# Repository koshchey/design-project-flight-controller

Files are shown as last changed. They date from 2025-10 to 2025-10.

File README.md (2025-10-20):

# Indoor Surveillance Drone – ELEC5552 Team 04 (UWA)

**Authors:** Sofia Khokhlenok (23099635), Sunny Guo (23345534)  
**Unit:** ELEC5552  
**Project Partners:** Michal Zawierta & Dilusha Silva, UWA Aviation Labs  
**Supervisor:** Jega Gurusamy  
**Team Number:** 04  

*Final Design Report - Version 2*

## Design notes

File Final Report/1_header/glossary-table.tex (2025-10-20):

\section*{Acronyms}
\renewcommand{\arraystretch}{1.2} % optional: adjust row spacing

\begin{tabular}{p{0.2\textwidth} p{0.3\textwidth} | p{0.2\textwidth} p{0.3\textwidth}}
\textbf{Acronym} & \textbf{Definition} & \textbf{Acronym} & \textbf{Definition} \\
\hline
IMU & Inertial Measurement Unit & UAV & Unmanned Aerial Vehicle \\
ToF & Time-of-Flight Sensor & UWAAL & UWA Aviation Labs \\
I\textsuperscript{2}C & Inter-Integrated Circuit & PCB & Printed Circuit Board \\
SPI & Serial Peripheral Interface & IR & Infrared \\
UWA & The University of Western Australia & QFD & Quality Function Deployment \\
LiPo & Lithium Polymer battery & NGO & Need, Goals, Objectives \\
PWM & Pulse Width Modulation & GPS & Global Positioning System \\
ESD & Electrostatic Discharge & MCU & Microcontroller \\
ESP32 & Espressif ESP32-Wroom Microcontroller & USB & Universal Serial Bus \\
MPU6050 & MEMS Accelerometer and Gyroscope IC & DC & Direct Current \\
wpa2 & Wi-Fi Protected Access 2 & ESP-IDF & Espressif IoT Development Framework \\
PID & Proportional-Integral-Derivative & RTOS & Real Time Operating System \\
IC & Integrated Circuit & MOSFET & Metal-Oxide-Semiconductor FET \\
AHRS & Attitude and Heading Reference System & UART & Universal Asynchronous RX/TX \\
EMI & Electromagnetic Interference & SCL & Serial Clock Line \\
SDA & Serial Data Line & LDO & Low Dropout Regulator \\
JST & Japan Solderless Terminal Connector & LED & Light Emitting Diode \\
FOV & Field of View & PETG & Polyethylene Terephthalate Glycol \\
RF & Radio Frequency & RC & Resistor-Capacitor \\
ISR & Interrupt Service Routine & ESC & Electronic Speed Controller \\
HTML & HyperText Markup Language &  &  \\
\end{tabular}

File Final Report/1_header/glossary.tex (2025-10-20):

\newacronym{imu}{IMU}{Inertial Measurement Unit}
\newacronym{tof}{ToF}{Time-of-Flight Sensor}
\newacronym{i2c}{I\textsuperscript{2}C}{Inter-Integrated Circuit}
\newacronym{spi}{SPI}{Serial Peripheral Interface}
\newacronym{uwa}{UWA}{The University of Western Australia}
\newacronym{lipo}{LiPo}{Lithium Polymer battery}
\newacronym{pwm}{PWM}{Pulse Width Modulation}
\newacronym{esd}{ESD}{Electrostatic Discharge}
\newacronym{esp32}{ESP32}{Espressif ESP32-Wroom Microcontroller Module}
\newacronym{mpu6050}{MPU6050}{MEMS Accelerometer and Gyroscope IC}
\newacronym{uav}{UAV}{Unmanned Aerial Vehicle}
\newacronym{uwaal}{UWAAL}{UWA Aviation Labs}
\newacronym{pcb}{PCB}{Printed Circuit Board}
\newacronym{ir}{IR}{Infrared}
\newacronym{qfd}{QFD}{Quality Function Deployment}
\newacronym{ngo}{NGO}{Need, Goals, Objectives}
\newacronym{gps}{GPS}{Global Positioning System}
\newacronym{mcu}{MCU}{Microcontroller}
\newacronym{usb}{USB}{Universal Serial Bus}
\newacronym{dc}{DC}{Direct Current}
\newacronym{wpa2}{WPA2}{Wi-Fi Protected Access 2}
\newacronym{esp-idf}{ESP-IDF}{Espressif IoT Development Framework}
\newacronym{pid}{PID}{Proportional-Integral-Derivative}
\newacronym{rtos}{RTOS}{Real Time Operating System}
\newacronym{ic}{IC}{Integrated Circuit}
\newacronym{mosfet}{MOSFET}{Metal-Oxide-Semiconductor Field-Effect Transistor}
\newacronym{ahrs}{AHRS}{Attitude and Heading Reference System}
\newacronym{uart}{UART}{Universal Asynchronous Receiver/Transmitter}
\newacronym{emi}{EMI}{Electromagnetic Interference}
\newacronym{scl}{SCL}{Serial Clock Line}
\newacronym{sda}{SDA}{Serial Data Line}
\newacronym{ldo}{LDO}{Low Dropout Regulator}
\newacronym{jst}{JST}{Japan Solderless Terminal Connector}
\newacronym{led}{LED}{Light Emitting Diode}
\newacronym{fov}{FOV}{Field of View}
\newacronym{petg}{PETG}{Polyethylene Terephthalate Glycol}
\newacronym{rf}{RF}{Radio Frequency}
\newacronym{rc}{RC}{Resistor-Capacitor}
\newacronym{isr}{ISR}{Interrupt Service Routine}
\newacronym{esc}{ESC}{Electronic Speed Controller}
\newacronym{html}{HTML}{HyperText Markup Language}

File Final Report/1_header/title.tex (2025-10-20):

\begin{titlepage}

\noindent\rule{\textwidth}{0.5pt}
\begin{flushright}
    \textbf{UWA ELEC5552}
\end{flushright}
\rule{\textwidth}{0.5pt}

\vspace{2cm}

\thispagestyle{empty}

\begin{center}
    {\Huge \textbf{Indoor Surveillance Drone}} \\[0.75cm]
    {\Large ELEC5552 Team 04} \\[1.5cm]

    \textsc{Author(s):} \\[0.5cm]

    \begin{tabular}{@{}c@{\hskip 1cm}c@{}}
        \textbf{Sofia Khokhlenok} & \textbf{Sunny Guo} \\[0.2cm]
        (23099635) & (23345534) \\
    \end{tabular} \\[1.5cm]

    {\Large \textbf{Final Design Report}} \\[0.5cm]
\end{center}

\vspace{1.5cm}

\begin{center}
\begin{tabular}{rl}
\textsc{Project Partners:} & Michal Zawierta \& Dilusha Silva, UWA Aviation Labs \\
\textsc{UWA Supervisor:} & Jega Gurusamy \\
\textsc{Team Number:} & 04 \\
\textsc{Meeting Time:} & Thursday, 10AM \\
\textsc{Word Count:} & 8568 \\
\textsc{Word Limit:} & 10~000 \\
\textsc{Version:} & 2 \\
\end{tabular}
\end{center}

\vfill

\begin{center}
    \large \today
\end{center}

\end{titlepage}

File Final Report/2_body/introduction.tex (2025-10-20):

\glspl{uav}, commonly referred to as drones, have become essential tools across a wide range of applications, including surveying, inspection, and research. Their ability to operate in confined or inaccessible environments makes them particularly valuable for close-range observation and monitoring tasks. Unlike outdoor drones that rely on satellite-based positioning systems such as GPS, indoor platforms must depend entirely on onboard sensing, control algorithms, and communication systems to maintain stability and navigate safely. Operating in enclosed environments presents additional challenges, including limited spatial awareness, airflow disturbances, and increased safety risks due to proximity to structures and personnel. Consequently, the design of an indoor \gls{uav} demands careful consideration of system architecture, control robustness, and physical safety features. 

\begin{figure}[H]
    \centering
    \captionsetup{justification=centering, margin=1cm}
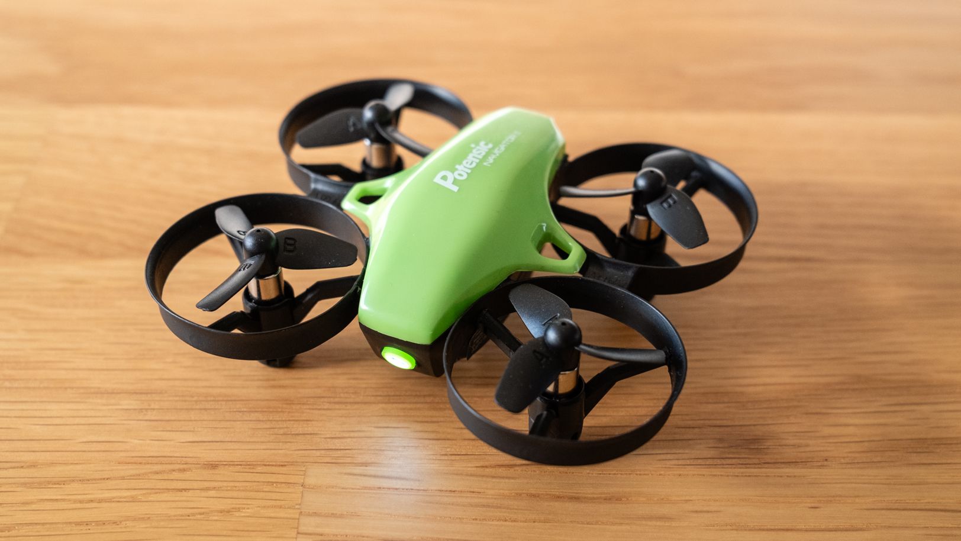
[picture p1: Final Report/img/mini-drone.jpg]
    
    \caption{Miniature Drone \cite{abbott2024}}
\end{figure}

The \gls{uwaal} has commissioned the development of an autonomous indoor drone capable of stable flight within confined environments. The system will be used to survey and inspect indoor areas such as garages and laboratories, following predefined flight paths while maintaining altitude and position despite external airflow disturbances. It must integrate sensing, control, communication, and power management within a compact and lightweight platform, designed from first principles to ensure safety, efficiency, and reliability. This project explores the design and implementation of such a platform, aligning with \gls{uwaal}’s objective to develop a safe, functional, and adaptable indoor drone for future research and educational applications. 

\subsection{Scope of This Report}

This report outlines the process undertaken to design and implement a functional indoor \gls{uav} for operation within confined environments. It defines the technical, safety, and regulatory boundaries within which the project was executed, as well as the methods used to evaluate performance against client-approved requirements. The scope covers system-level design, hardware and firmware integration, testing, and validation to ensure stable flight, effective altitude control, reliable communication, and essential safety functionality. 

The document also presents the rationale behind key design choices and the underlying system architecture. It details specific design aspects, including component selection, \gls{pcb} schematic design and layout, flight control algorithms, and safety mechanisms, while addressing relevant standards for electrical safety, risk management, and compliance. Consideration is given to manufacturability, maintainability, and adherence to cost and resource constraints. Beyond immediate development outcomes, the report establishes a framework that supports future extensions of the platform within the \gls{uwaal}. 

\subsection{Purpose of the Design}

The primary objective of this project is to design, develop, and validate a low-cost indoor drone capable of achieving stable flight and hovering performance without GPS-based navigation. The system is intended for use within the \gls{uwaal} to perform autonomous operations while maintaining a specified altitude and compensating for environmental disturbances such as localised airflow. 

\begin{figure}[H]
    \centering
    \captionsetup{justification=centering, margin=1cm}
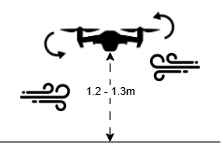
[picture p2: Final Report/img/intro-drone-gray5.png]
    
    \caption{Surveillance Drone Diagram}
\end{figure}

The proposed system architecture features a custom-designed \gls{pcb} flight controller integrating onboard power distribution, sensing, and control modules. Flight stabilisation and altitude control are achieved through sensor fusion of inertial and distance measurements processed via onboard control algorithms. The design incorporates safety features such as shrouded propellers or propeller guards, low-battery auto-landing capability, and a failsafe mechanism that triggers a controlled landing or motor shutdown following a communication loss exceeding thirty seconds. The drone operates on 1S or 2S lithium-polymer batteries with a maximum capacity of 800~mAh and must sustain a minimum flight duration of three minutes. All components and materials conform to the allocated project budget of AUD~\$350. The overarching goal is to deliver a robust, safe, and open-source indoor drone platform that satisfies all operational, safety, and budgetary requirements. 

\subsection{Background}

\glspl{uav} combine sensing, computation, and actuation to achieve controlled flight through coordinated motor thrust. Their operation depends on precise feedback control systems that maintain stability and orientation while responding to pilot or autonomous commands. This is typically accomplished using onboard microcontrollers running real-time control algorithms that process data from inertial and range sensors to dynamically adjust motor outputs.

\begin{figure}[H]
    \centering
    \captionsetup{justification=centering, margin=1cm}
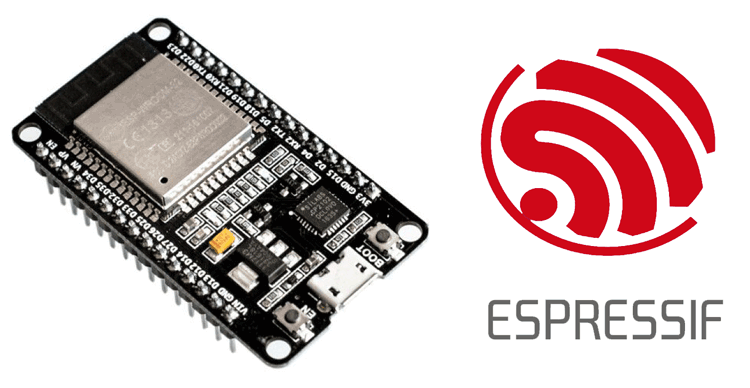
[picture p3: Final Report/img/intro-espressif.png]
    
    \caption{Espressif ESP32 DevKit~\cite{iotdesignpro2019}}
\end{figure}

\pagebreak

The ESP32 microcontroller has emerged as a compact and cost-effective solution for such systems, integrating dual-core processing, Wi-Fi connectivity, and sufficient computational power to manage both flight control and communication tasks. Its compatibility with open-source frameworks such as Espressif’s \gls{esp-idf} enables flexible low-level implementation of control loops, sensor fusion, and telemetry within a single embedded platform.

In parallel, advances in printed circuit board (\gls{pcb}) design allow integration of flight electronics, power management, and motor drivers onto lightweight, custom boards that minimise wiring and improve reliability. 

\begin{figure}[H]
    \centering
    \captionsetup{justification=centering, margin=1cm}
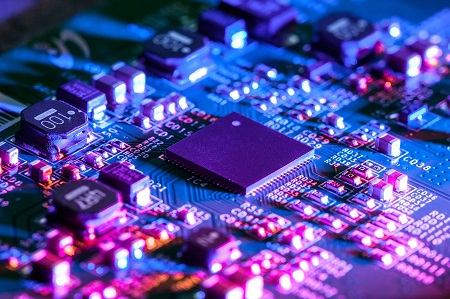
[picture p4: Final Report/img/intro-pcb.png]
    
    \caption{Printed Circuit Board \cite{mistral2020}}
\end{figure}

Together, these developments enable the creation of small-scale, low-cost autonomous drones capable of stable flight and sensor-based navigation for educational, research, and experimental applications.

\subsection{Summary of Contributions}

\begin{table}[H]
\centering
\caption{Team Member Contribution Breakdown}
\renewcommand{\arraystretch}{1.2}
\begin{tabular}{@{}lcc@{}}
\toprule
\textbf{Task} & \textbf{Sofia Khokhlenok (\%)} & \textbf{Sunny Guo (\%)} \\ 
\midrule
Conception & 50 & 50 \\
Research & 60 & 40 \\
Requirement Development & 50 & 50 \\
System Design & 70 & 30 \\
System Architecture & 50 & 50 \\
Hardware Development & 20 & 80 \\
Firmware Development & 90 & 10 \\
PCB Research & 40 & 60 \\
PCB/Frame Prototyping & 20 & 80 \\
Purchasing Electronic Materials & 50 & 50 \\
Frame Design & 15 & 85 \\
Software Debugging and Testing & 80 & 20 \\
Hardware Debugging and Testing & 20 & 80 \\
Overall Prototype Testing & 50 & 50 \\
Management and Organization & 80 & 20 \\
Final Report & 55 & 45 \\
\textbf{Average} & 50 & 50 \\
\bottomrule
\end{tabular}
\end{table}

\subsection{Report Structure}
This report provides a comprehensive overview of the design, development, and evaluation of the autonomous ESP32-based indoor surveillance drone. 

\textbf{Section~1} introduces the project, outlining its scope, purpose, background, and summary of contributions. It also describes the overall report structure to guide the reader. 

\textbf{Section~2} presents the detailed design process, including system requirements, overall and subsystem architecture (hardware, firmware, and justification), and individual design elements such as PCB components, frame design, and firmware modules. It further describes testing procedures—covering hardware verification, stationary and dynamic testing—as well as system integration, stakeholder engagement, safety, ethical considerations, and risk analysis. The section concludes with assembly procedures, design outputs, and final cost breakdowns.

\textbf{Section~3} outlines recommendations for future improvements and potential extensions of the system. 

\textbf{Section~4} serves as a user manual, providing detailed instructions for operation, maintenance, and troubleshooting. 

\textbf{Section~5} lists all referenced materials and supporting documentation. 

Finally, \textbf{the Appendices} contain supplementary materials, including design constraints, requirements updates, prototype details, additional figures, and complete firmware source code listings.

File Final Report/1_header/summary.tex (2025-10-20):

The project presents the design and implementation of an autonomous indoor \gls{uav} for the \gls{uwaal}. The system is intended to operate safely in confined spaces, such as laboratories and workshops, performing inspection and monitoring tasks without reliance on \gls{gps}. The drone integrates sensing, control, communication, and power management on a compact platform built around a custom \gls{pcb} and an \gls{esp32} running the \gls{esp-idf} framework. Key features include stabilisation control systems, onboard sensor fusion, a modular frame with propeller guards, and a real-time telemetry and control interface.

All hardware and firmware subsystems have been implemented and verified individually. The architecture, control logic, and safety mechanisms operate as intended; however, stable flight has not yet been achieved due to motor inconsistencies and limited dynamic testing. With motor replacement, \gls{pid} tuning, and further validation, the system is expected to meet its performance and safety objectives. The project establishes a solid foundation for ongoing development, providing a functional and extensible platform for future research within the \gls{uwaal}.

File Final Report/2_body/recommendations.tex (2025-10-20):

As of the writing of this report, the drone prototype is not yet capable of stable flight. All essential subsystems and components have been implemented and verified individually. The hardware has been tested and is operational, except for some inconsistencies with the motors, which may require replacement. The firmware architecture and control logic function correctly; however, the closed-loop performance of the \gls{pid} controller has not been validated due to limited testing opportunities. With further refinement and testing, the project goals can be fully achieved.

\subsection*{Recommendations for Achieving Project Goals}

\begin{itemize}
    \item \textbf{Motor Replacement and Testing:} Replace the motors and conduct testing to ensure sufficient thrust and balanced torque. Document results in the Verification and Validation (V\&V) table.
    
    \item \textbf{PID Tuning:} Perform PID tuning under hover conditions once stable thrust is achieved. Adjust gains incrementally and log system responses to optimise stability and control.
    
    \item \textbf{Assembly and Connectivity:} Simplify the mechanical and electrical assembly. Use modular connectors or streamlined wiring layouts to reduce manual work and improve reliability.
    
    \item \textbf{Sensor Upgrade:} Consider replacing the \gls{mpu6050} with a more modern \gls{imu} to improve data accuracy, reduce noise, and enhance stability during flight.
    
    \item \textbf{Future Hardware Improvements:} Evaluate brushless motors, electronic speed controllers (\gls{esc}), and higher-voltage batteries to improve thrust and control precision while maintaining safety with the current frame and software limits.
\end{itemize}

Overall, the system foundation is solid. With incremental hardware replacements, \gls{pid} optimisation, and moderate design refinements, the drone can achieve stable and reliable flight and meet the original project objectives.

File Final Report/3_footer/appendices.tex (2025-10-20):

\subsection{Constraints}
\label{app:constraints}

\begin{table}[H]
\centering
\caption{Constraints for Drone Design (Updated)}
\label{tab:constraints}
\begin{tabular}{|>{\centering\arraybackslash}p{0.05\textwidth} | >{\centering\arraybackslash}p{0.13\textwidth} | p{0.42\textwidth} | p{0.30\textwidth}|}
\hline
\rowcolor{gray!15}
\textbf{No.} & \textbf{Constraint} & \textbf{Description} & \textbf{Assumptions} \\
\hline
C.1 & Weight & The total weight of the drone must allow for continuous and stable flight. & The quad-mounted motors can support a maximum payload of 60\,g. \\
\hline
C.2 & Software & Only free and open-source flight controller software shall be used. & The firmware will incorporate third-party open-source code, which will be modified to suit the application (e.g., autonomy and feedback). \\
\hline
C.3 & Operating Environment & The drone is limited to operation within a fixed indoor area containing immovable fixtures (e.g., wall-mounted displays). & -- \\
\hline
C.4 & Budget & The design and construction of the drone shall remain within the allocated project budget. & -- \\
\hline
C.5 & Network Speed & Wireless bandwidth and latency may limit the system’s ability to stream live video. & Streaming will occur via \gls{uwa} Wi-Fi or a mobile hotspot. \\
\hline
C.6 & Safety & The drone must be safe for operation by the user and must not pose any physical risk to personnel. & -- \\
\hline
C.7 & Sensor Selection & Available sensors (such as \gls{imu} and \gls{tof}) are constrained by cost, availability, and ability to interface with the ESP32 microcontroller. & Supported interfaces include \gls{uart}, \gls{i2c}, and \gls{spi}. \\
\hline
\end{tabular}
\end{table}

\subsection{Additional Requirements}
\label{app:additional_req}

\begin{table}[H]
\centering
\caption{Additional Requirements}
\begin{tabular}{|>{\centering\arraybackslash}p{0.1\textwidth} | p{0.8\textwidth}|}
\hline
\rowcolor{gray!15}
\textbf{No.} & \textbf{Requirement} \\
\hline
R.16 & The \gls{pcb} shall include custom motor drivers. \\
\hline
R.19 & The drone shall be able to fly for a minimum of 3 minutes. \\
\hline
R.28 & The surveillance camera shall stream a live camera feed. \\
\hline
R.26 & The UI shall include a battery level monitoring system for detecting low battery levels. \\
\hline
R.29 & The surveillance camera shall record video for playback. \\
\hline
R.25 & The UI shall include an error diagnostic and feedback system. \\
\hline
R.6  & The hovering altitude shall be adjustable prior to operation, within a range of 0.5 to 2 metres. \\
\hline
A.R.2 & The drone’s operational capabilities shall be powered by a single battery. \\
\hline
A.R.4 & A comprehensive operation manual and user guide shall be provided to the client for use, understanding, and further development. \\
\hline
A.R.6 & Placement of components on the \gls{pcb} shall minimise signal distortion and heat generation to ensure accurate flight paths and predictable behaviour. \\
\hline
A.R.7 & The drone shall feature a visual (\gls{led}) or audible warning system to alert personnel during flight initiation. \\
\hline
A.R.8 & The drone shall provide a UI alert in cases of overheating. \\
\hline
A.R.9 & The drone shall include LEDs to indicate charging mode. \\
\hline
A.R.10 & The drone shall feature visual or UI indicators showing when it is powering down or operating autonomously. \\
\hline
\end{tabular}
\end{table}

%----------------------------------------------------------%
\pagebreak
\subsection{Verification and Validation}
\label{app:v-and-v}

\begin{figure}[H]
    \centering
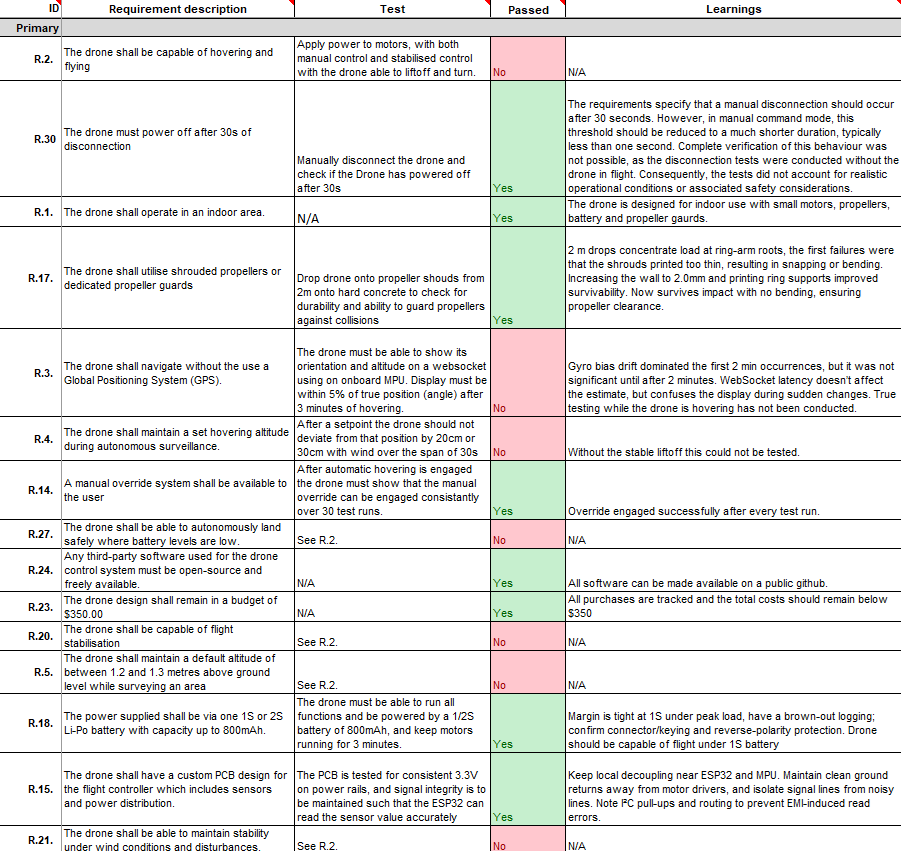
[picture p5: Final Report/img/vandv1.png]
    
\end{figure}

\begin{figure}[H]
    \centering
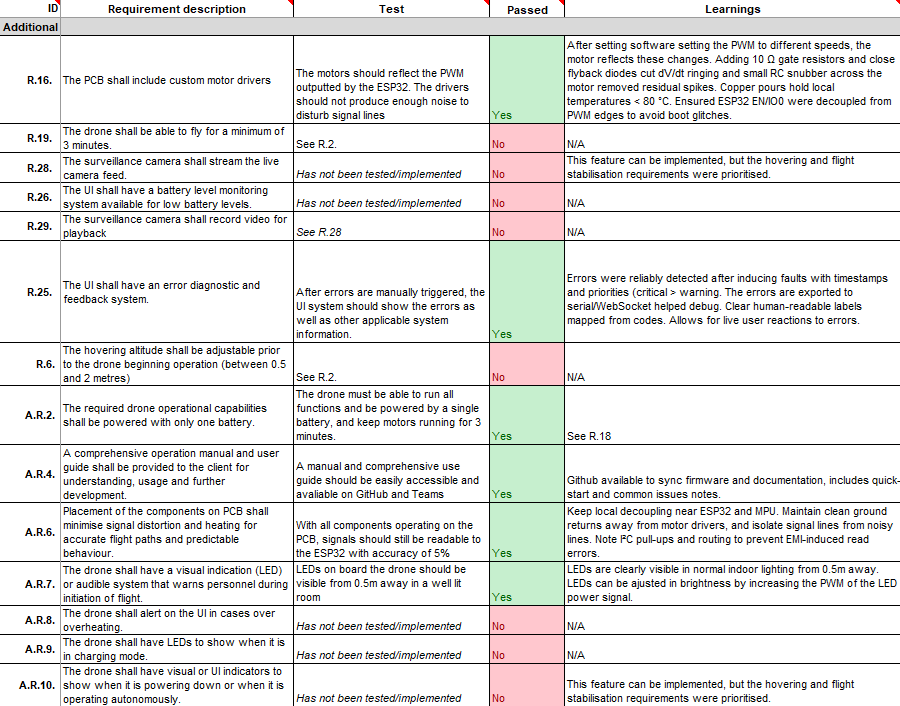
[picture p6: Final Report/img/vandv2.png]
    
\end{figure}

%----------------------------------------------------------%
\pagebreak
\subsection{Hardware Prototypes}
\label{app:pcb-prototypes}

\subsubsection{PCB Prototype 1.0}

\begin{figure}[H]
    \centering
    \begin{subfigure}[b]{0.45\linewidth}
        \centering
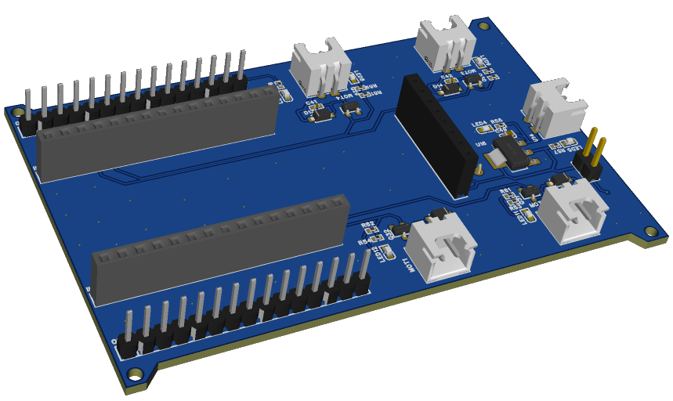
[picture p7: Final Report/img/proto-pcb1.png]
        
        \caption{Overview}
        \label{fig:pcb1-overview}
    \end{subfigure}
    \hfill
    \vfill
    \begin{subfigure}[b]{0.4\linewidth}
        \centering
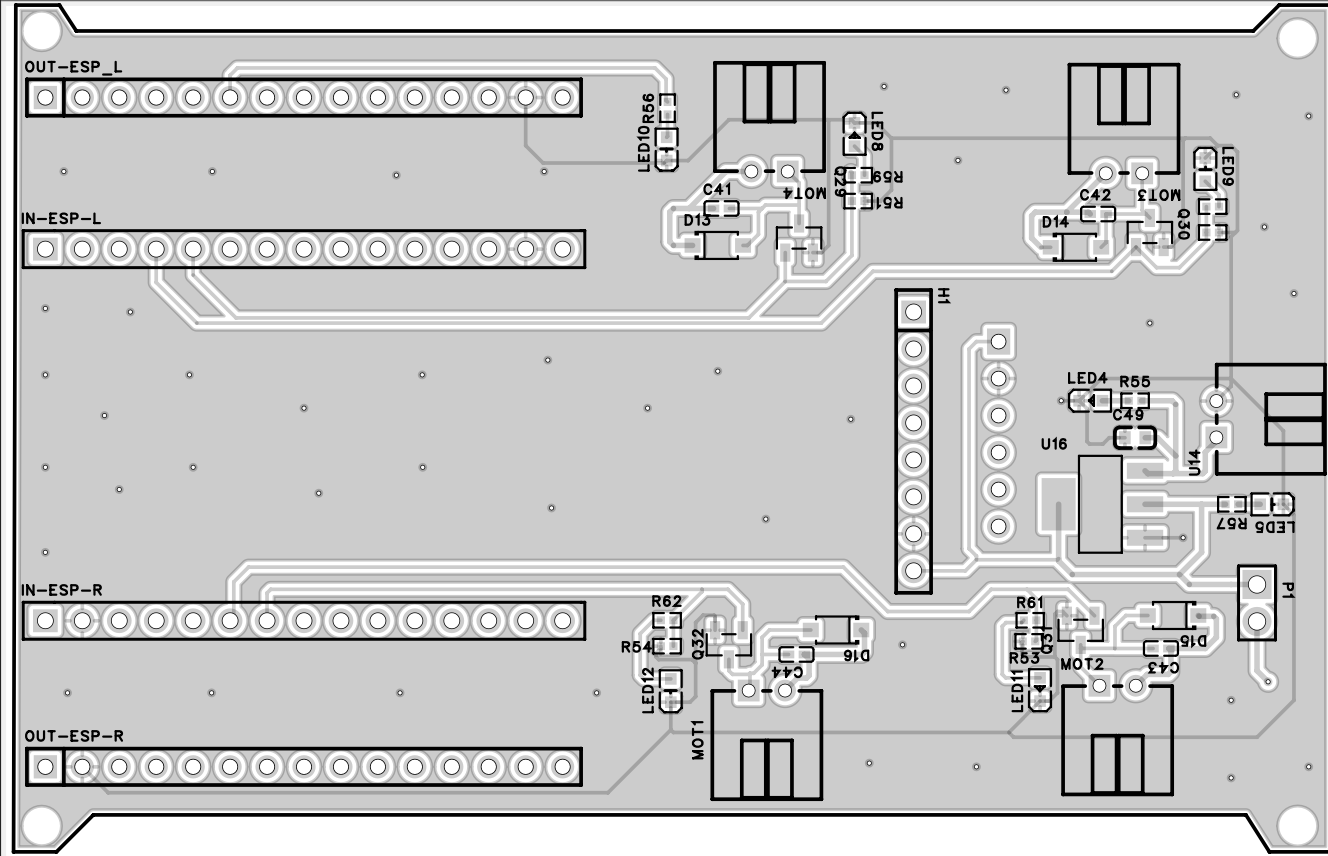
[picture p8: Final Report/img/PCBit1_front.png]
        
        \caption{Front Side}
        \label{fig:pcb1-front}
    \end{subfigure}
    \hfill
    \begin{subfigure}[b]{0.4\linewidth}
        \centering
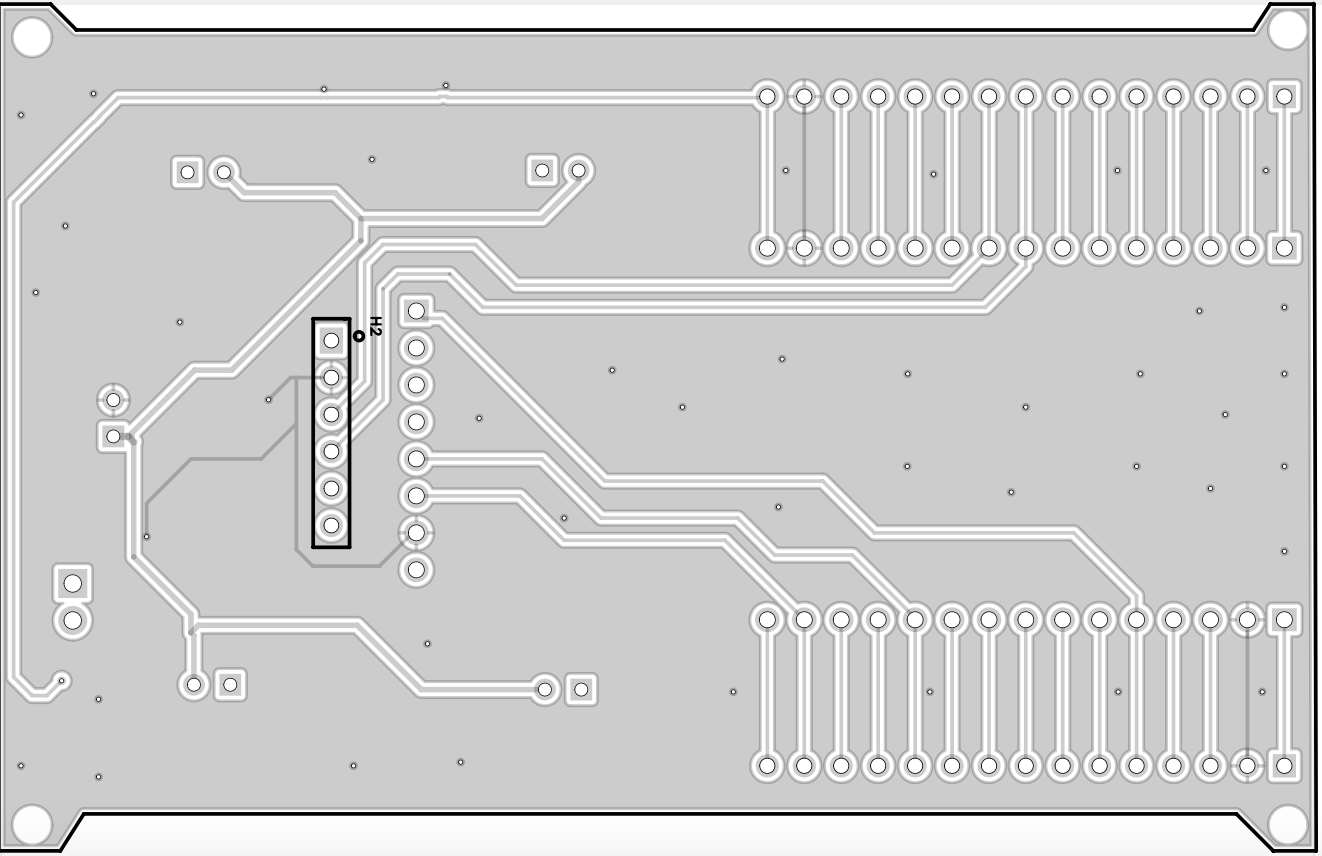
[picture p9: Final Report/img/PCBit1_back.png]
        
        \caption{Back Side}
        \label{fig:pcb1-back}
    \end{subfigure}
    \label{fig:pcb1}
\end{figure}

% \pagebreak
\subsubsection{PCB Prototype 2.0}

\begin{figure}[H]
    \centering
    \begin{subfigure}[b]{0.45\linewidth}
        \centering
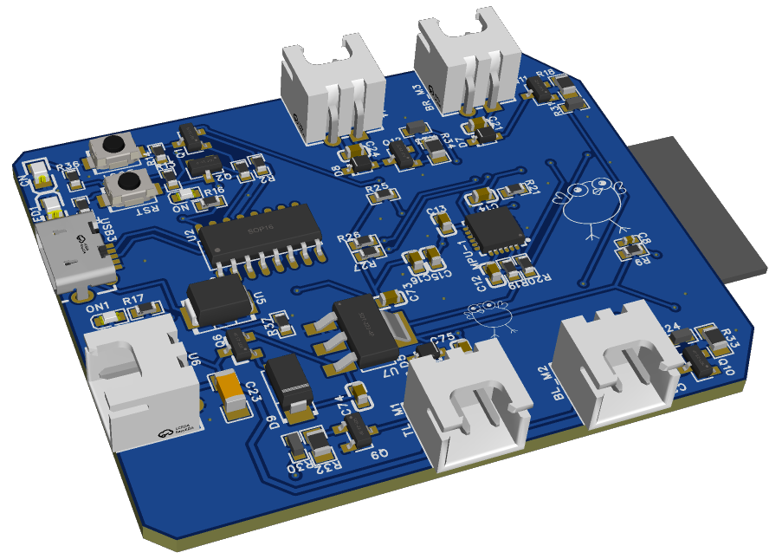
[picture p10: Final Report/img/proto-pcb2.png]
        
        \caption{Overview}
        \label{fig:pcb2-overview}
    \end{subfigure}
    \vfill
    \begin{subfigure}[b]{0.4\linewidth}
        \centering
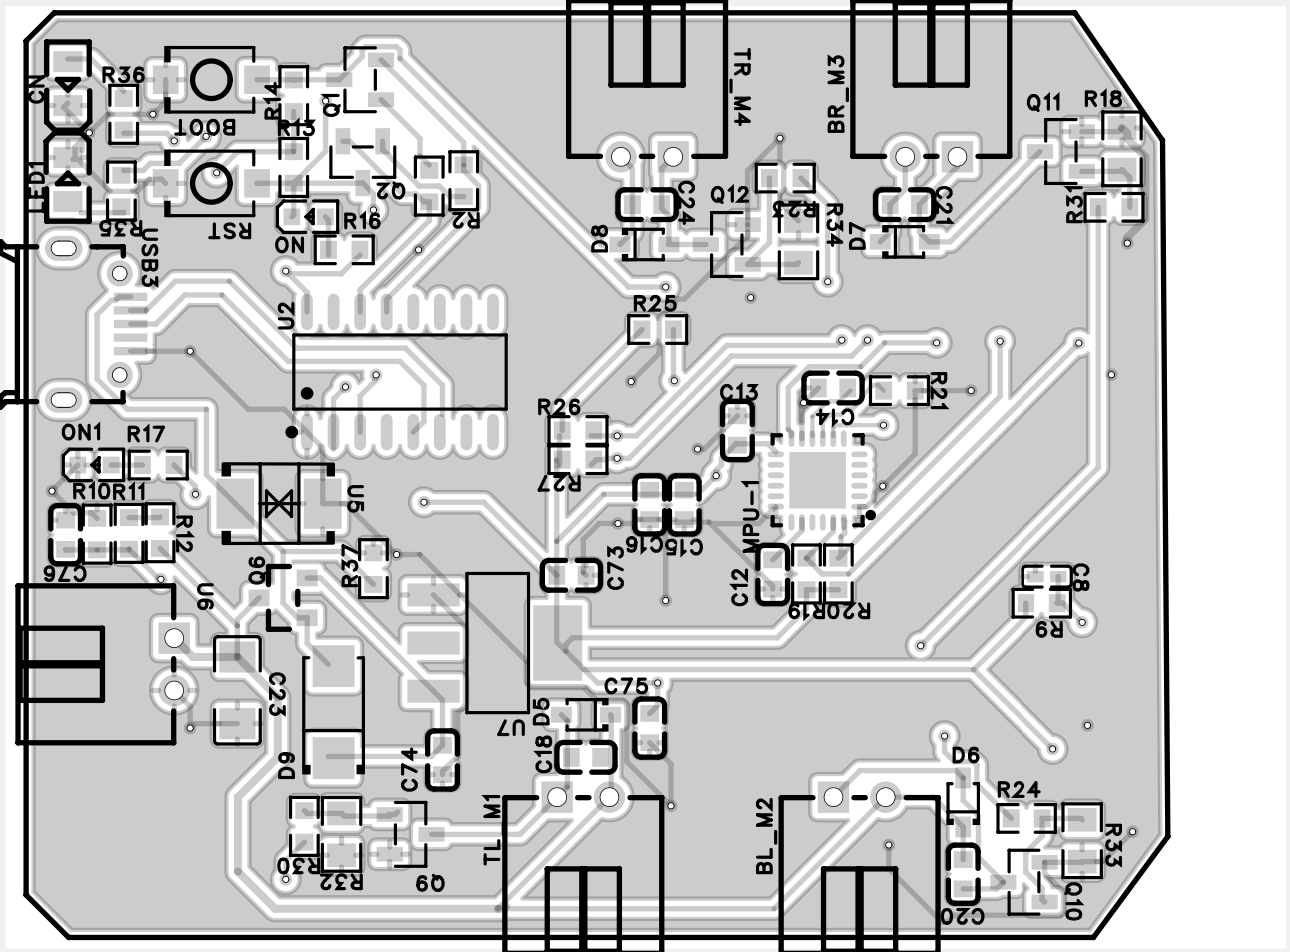
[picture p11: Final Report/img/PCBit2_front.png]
        
        \caption{Front Side}
        \label{fig:pcb2-front}
    \end{subfigure}
    \hfill 
    \begin{subfigure}[b]{0.4\linewidth}
        \centering
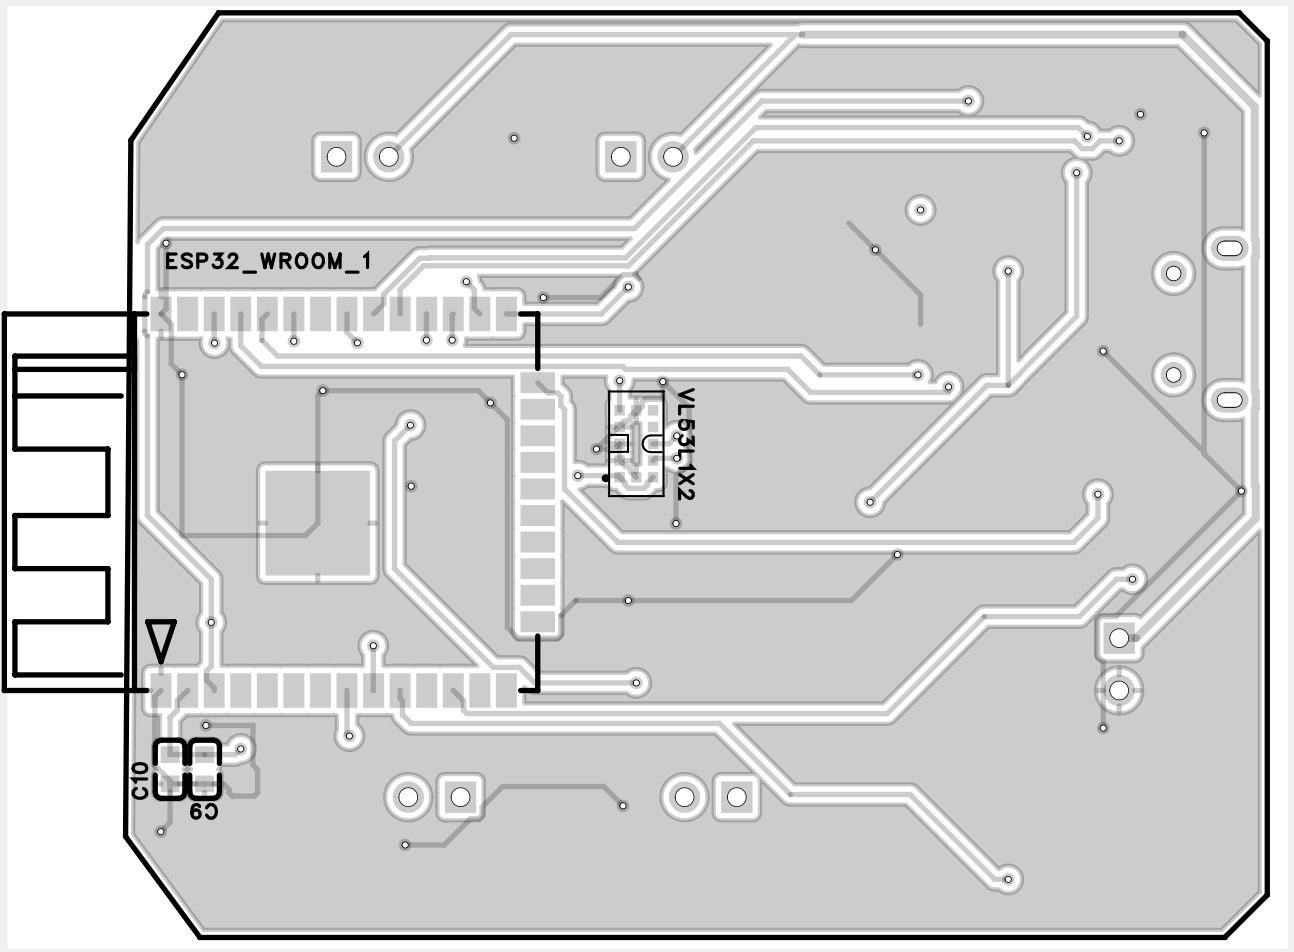
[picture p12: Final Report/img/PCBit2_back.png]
        
        \caption{Back Side}
        \label{fig:pcb2-back}
    \end{subfigure}
    \label{fig:pcb2}
\end{figure}

\pagebreak
\subsubsection{Frame Prototypes}

\begin{figure}[H]
    \centering
    % Prototype 1.0
    \begin{subfigure}[b]{0.48\linewidth}
        \centering
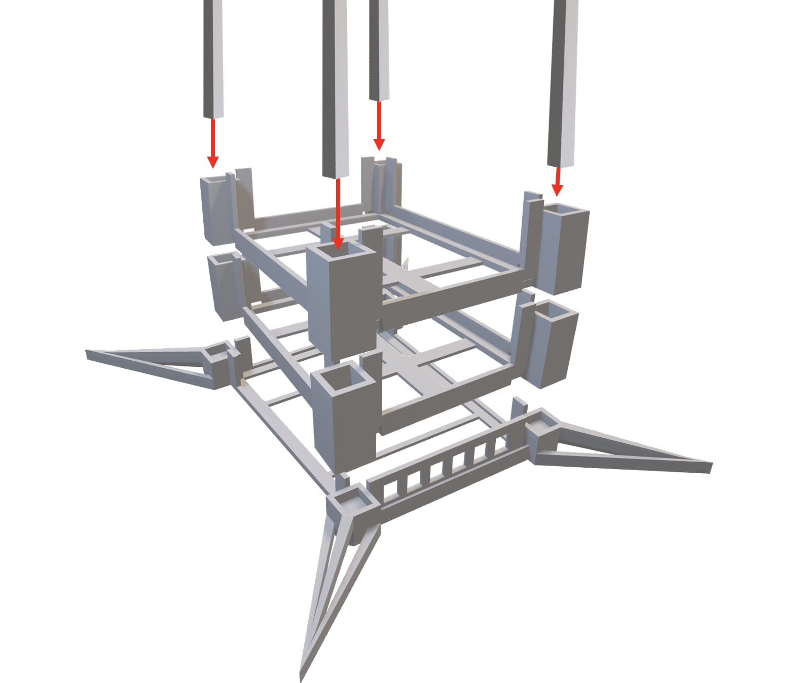
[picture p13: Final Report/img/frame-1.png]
        
        \caption{Prototype 1.0}
        \label{fig:frame-proto1}
    \end{subfigure}
    \hfill
    % Prototype 2.0
    \begin{subfigure}[b]{0.48\linewidth}
        \centering
        
        \caption{Prototype 2.0}
        \label{fig:frame-proto2}
    \end{subfigure}
    \hfill
    % Prototype 3.0 (front)
    \begin{subfigure}[b]{0.48\linewidth}
        \centering
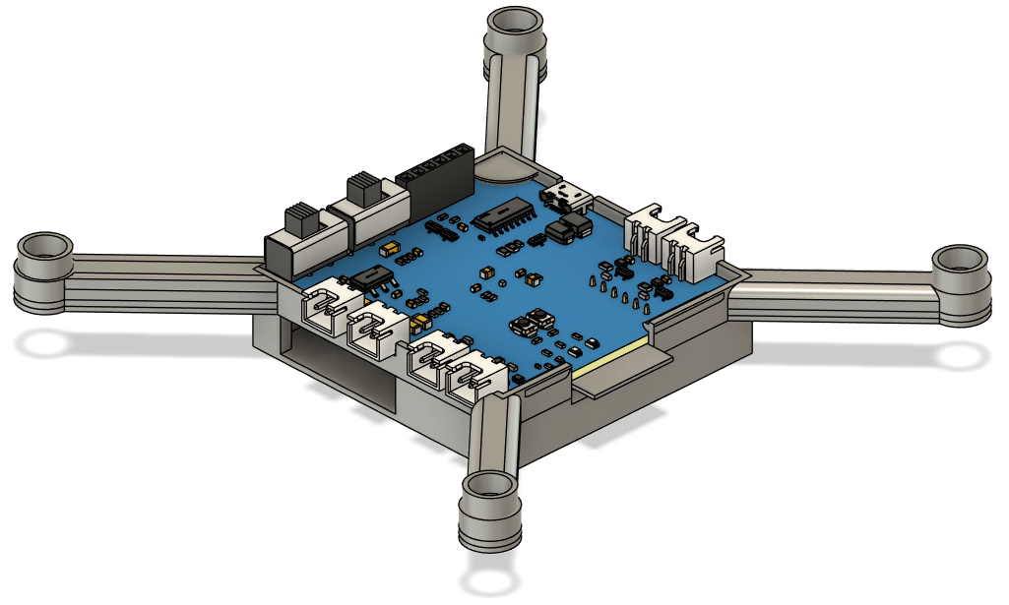
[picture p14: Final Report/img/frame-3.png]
        
        \caption{Prototype 3.0 Front}
        \label{fig:frame-proto3-front}
    \end{subfigure}
    % Prototype 3.0 (back) on a new line
    \vspace{0.3cm}
    \begin{subfigure}[b]{0.48\linewidth}
        \centering
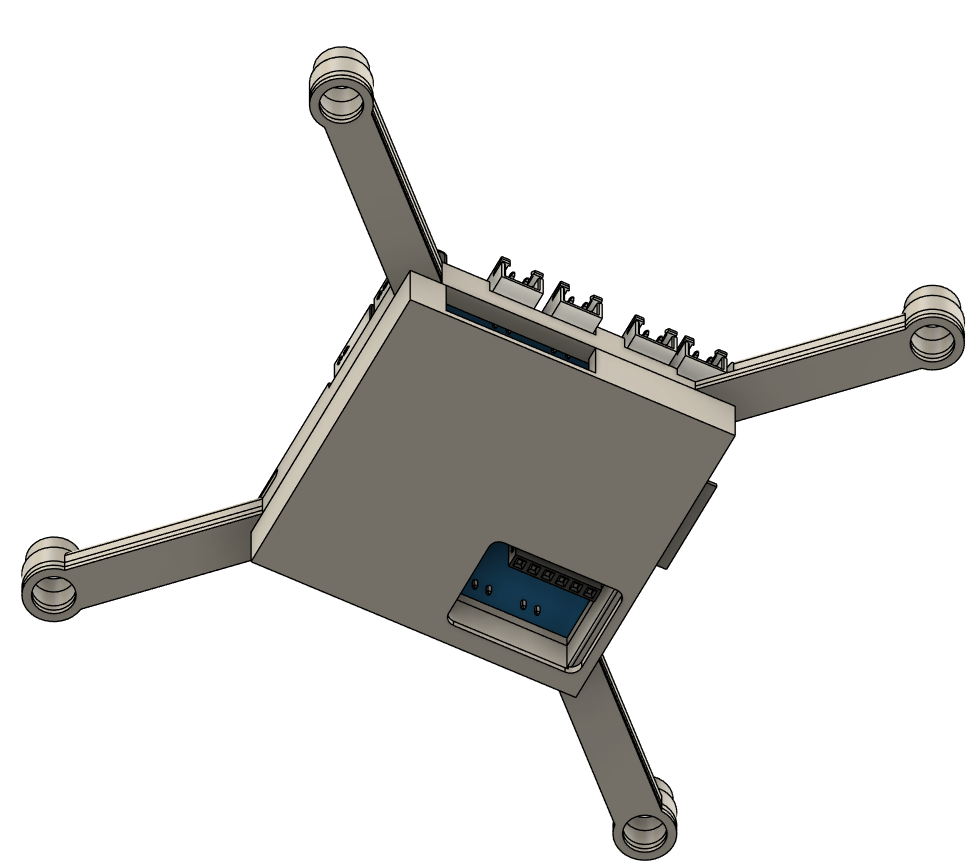
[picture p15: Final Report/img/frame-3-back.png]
        
        \caption{Prototype 3.0 Back}
        \label{fig:frame-proto3-back}
    \end{subfigure}
    % \caption{Development of frame prototypes 1.0 to 3.0, showing front and back views of the final iteration.}
    \label{fig:frame-prototypes}
\end{figure}

\pagebreak
\subsubsection{Assembled Prototype 1.0}

\begin{figure}[H]
    \centering
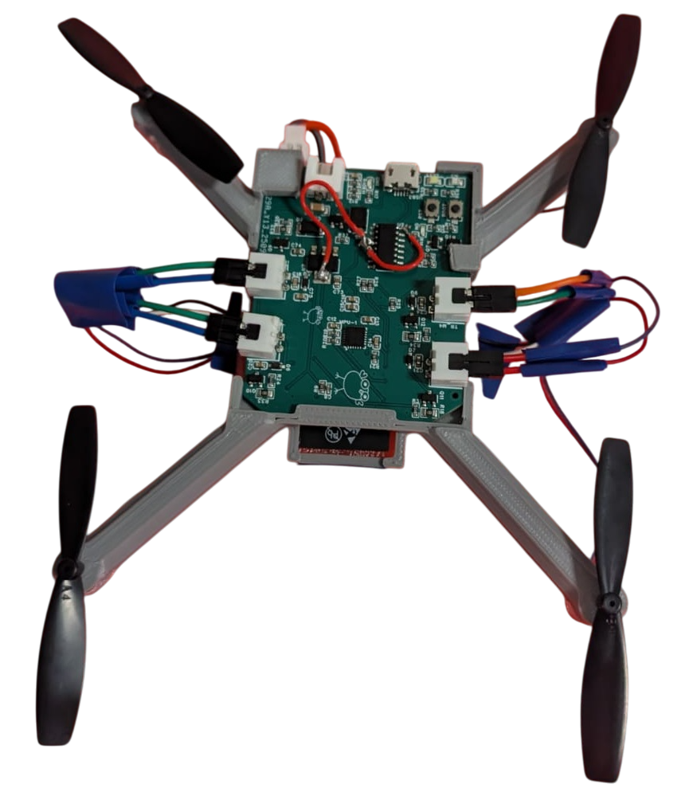
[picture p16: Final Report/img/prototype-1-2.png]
    
\end{figure}

\subsubsection{Assembled Prototype 2.0 For Testing}

\begin{figure}[H]
    \centering
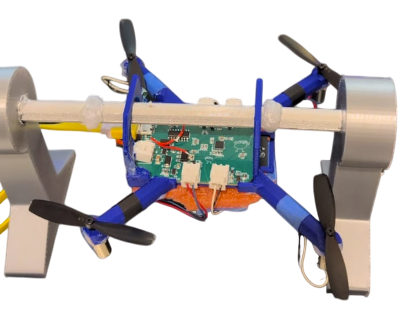
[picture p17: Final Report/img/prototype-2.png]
    
\end{figure}

%----------------------------------------------------------%
\subsection{WebSocket Page}
\label{app:websocket}

\begin{figure}[H]
    \centering
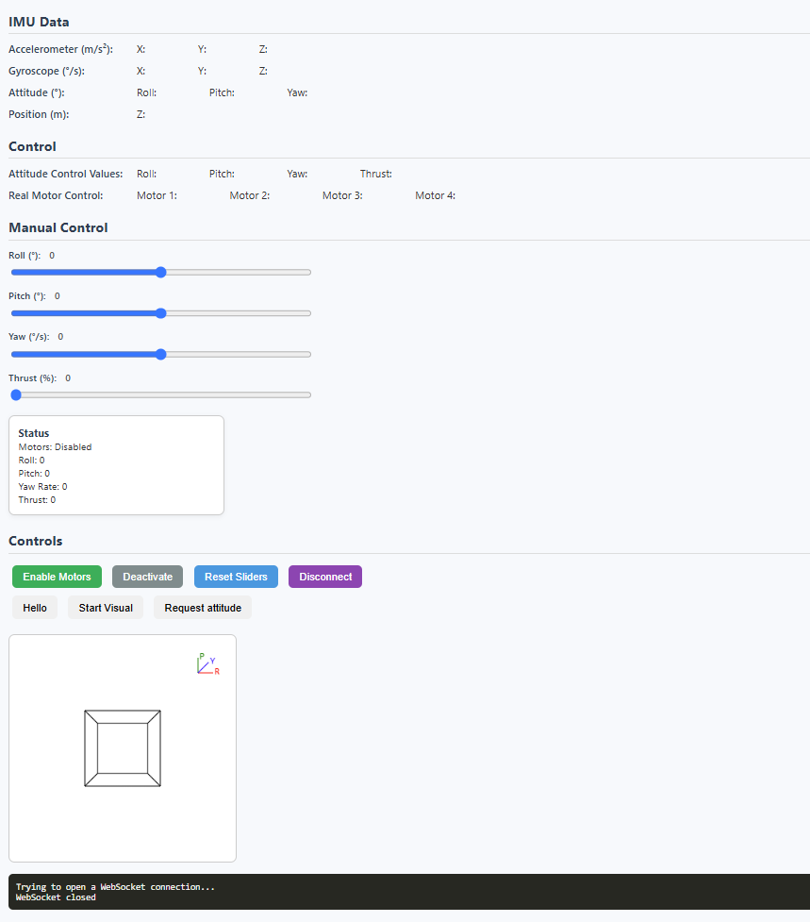
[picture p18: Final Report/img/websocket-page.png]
    
    \caption{WebSocket Client Web Page}
\end{figure}

%----------------------------------------------------------%
\pagebreak

\subsection{Stakeholder Engagement}
\label{app:stakeholder-engagement}

\begin{table}[H]
\centering
\caption{Client Meetings, Information Sessions, and Technical Queries - Summary (Weeks 1-5)}
\begin{tabular}{|p{2cm}|p{9.5cm}|p{3cm}|}
\hline
\textbf{Date / Week} & \textbf{Item / Notes} & \textbf{Priority / Additional Notes} \\ \hline
24/07/2025 (W1) & Open-source software must be used. & -- \\ \hline
 & Client requirements may be negotiated with the client. & -- \\ \hline
31/07/2025 (W2) & \textbf{Q1:} Desired action when drone encounters obstacle (stop, reverse, turn around). & Medium \\ \hline
 & \textbf{Client Response:} Stop and hover; shutdown if obstruction persists. Both options desirable. & -- \\ \hline
 & \textbf{Q2:} Requirements for drone movement patterns—preprogrammed or flexible. & High \\ \hline
 & \textbf{Client Response:} Preprogrammed patterns given 1-2 weeks before demo. Custom pattern: simple polygon. & Plan flexible design early \\ \hline
07/08/2025 (W3) & \textbf{Q3:} Two 1S batteries instead of one 2S? Max total capacity 800mAh? & Medium \\ \hline
 & \textbf{Client Response:} Only one battery allowed. Total capacity < 800mAh. & -- \\ \hline
 & Other relevant info: Reaction to wall/obstacles same; automatic obstacle detection and shutdown. & -- \\ \hline
15/08/2025 (W4) & No technical queries this week. & -- \\ \hline
23/08/2025 (W5) & \textbf{Q4:} Mounting IR sensor (VL53L0X) with perpendicular orientation to main PCB. Breakout allowed? & Medium \\ \hline
 & \textbf{Client Response:} Yes. & -- \\ \hline
 & \textbf{Q5:} Can we place coloured/reflective tape for start position? & Low \\ \hline
 & \textbf{Client Response:} Yes. & -- \\ \hline
\end{tabular}
\end{table}

\begin{table}[H]
\centering
\caption{Other Information - Summary (Weeks 1-5)}
\begin{tabular}{|p{2.5cm}|p{12cm}|}
\hline
\textbf{Date / Week} & \textbf{Item / Notes} \\ \hline
24/07/2025 (W1) &
Drifting should be below 10 cm before stabilisation.  \newline 
Object detection is for non-transparent objects only.  \newline 
Surveillance camera must record video and optionally allow hover height adjustment. \newline
Final testing location: MATH151. \newline
ESCs must be part of the PCB. \\ \hline
07/08/2025 (W3) &
No obstacles on ground during demo. \newline
Can use magnetometer and multiple MCU chips, particularly for camera. \newline Camera does not need to be ESP32-based \newline \\ \hline
\end{tabular}
\end{table}

%----------------------------------------------------------%
\pagebreak
\subsection{Requirements Update Summary (Week 6)}
\label{app:req-changes}

\subsubsection{Ranked Requirements - Proposed Changes}

\begin{table}[H]
\centering
\caption{Ranked Requirements Proposed Changes}
\begin{tabular}{|c|c|p{11cm}|}
\hline
\textbf{Rank} & \textbf{No.} & \textbf{Requirement Description} \\ \hline
1 & R.2 & The drone shall be capable of hovering and flying. \\ \hline
2 & R.30 & The drone must power off after 30s of disconnection. \\ \hline
3 & R.1 & The drone shall operate in an indoor area. \\ \hline
4 & R.17 & The drone shall utilise shrouded propellers or dedicated propeller guards. \\ \hline
5 & R.3 & The drone shall navigate without the use of GPS. \\ \hline
6 & R.4 & The drone shall maintain a set hovering altitude during autonomous surveillance. \\ \hline
7 & R.14 & A manual override system shall be available to the user. \\ \hline
8 & R.27 & The drone shall autonomously land safely when battery levels are low. \\ \hline
9 & R.24 & Any third-party software used for the drone control system must be open-source and freely available. \\ \hline
10 & R.7 & \textcolor{red}{\sout{The drone shall be able to navigate autonomously.}} \\ \hline
11 & R.11 & \textcolor{red}{\sout{The drone should be capable of detecting obstacles.}} \\ \hline
12 & R.12 & \textcolor{red}{\sout{The drone shall be capable of avoiding non-transparent obstacles (including walls) by stopping and hovering.}} \\ \hline
13 & R.23 & The drone design shall remain within a budget of \$350.00. \\ \hline
14 & R.20 & The drone shall be capable of flight stabilisation. \\ \hline
15 & R.5 & The drone shall maintain a default altitude of 1.2-1.3 metres above ground level while surveying an area. \\ \hline
16 & R.18 & The power supplied shall be via one 1S or 2S Li-Po battery with a capacity up to 800mAh. \\ \hline
17 & R.15 & The drone shall have a custom PCB design for the flight controller which includes sensors and power distribution. \\ \hline
18 & R.8 & \textcolor{red}{\sout{The drone shall follow a predefined path set before beginning operation.}} \\ \hline
19 & R.13 & \textcolor{red}{\sout{The drone shall power down if it detects an obstacle and the obstacle is not removed within a certain time limit.}} \\ \hline
20 & R.21 & The drone shall maintain stability under wind conditions and disturbances. \\ \hline
\end{tabular}
\end{table}

\begin{table}[H]
\centering
\caption{Ranked Requirements - Final}
\begin{tabular}{|c|c|p{11cm}|}
\hline
\textbf{Rank} & \textbf{No.} & \textbf{Requirement Description} \\ \hline
1 & R.2 & The drone shall be capable of hovering and flying. \\ \hline
2 & R.30 & The drone must power off after 30s of disconnection. \\ \hline
3 & R.1 & The drone shall operate in an indoor area. \\ \hline
4 & R.17 & The drone shall utilise shrouded propellers or dedicated propeller guards. \\ \hline
5 & R.3 & The drone shall navigate without the use of GPS. \\ \hline
6 & R.4 & The drone shall maintain a set hovering altitude during autonomous surveillance. \\ \hline
7 & R.14 & A manual override system shall be available to the user. \\ \hline
8 & R.27 & The drone shall autonomously land safely when battery levels are low. \\ \hline
9 & R.24 & Any third-party software used for the drone control system must be open-source and freely available. \\ \hline
10 & R.23 & The drone design shall remain within a budget of \$350.00. \\ \hline
11 & R.20 & The drone shall be capable of flight stabilisation. \\ \hline
12 & R.5 & The drone shall maintain a default altitude of 1.2-1.3 metres above ground level while surveying an area. \\ \hline
13 & R.18 & The power supplied shall be via one 1S or 2S Li-Po battery with a capacity up to 800mAh. \\ \hline
14 & R.15 & The drone shall have a custom PCB design for the flight controller which includes sensors and power distribution. \\ \hline
15 & R.21 & The drone shall maintain stability under wind conditions and disturbances. \\ \hline
\end{tabular}
\end{table}

\subsubsection{Additional Requirements - Proposed Changes}

\begin{table}[H]
\centering
\caption{Additional Requirements Proposed Changes}
\begin{tabular}{|c|p{11cm}|}
\hline
\textbf{No.} & \textbf{Description} \\ \hline
R.16 & The PCB shall include custom motor drivers. \\ \hline
R.19 & The drone shall be able to fly for a minimum of 3 minutes. \\ \hline
R.28 & The surveillance camera shall stream the live camera feed. \\ \hline
R.9 & \textcolor{red}{\sout{There shall be a predefined set of options for the drone flight.}} \\ \hline
R.26 & The UI shall have a battery level monitoring system available for low battery levels. \\ \hline
R.29 & The surveillance camera shall record video for playback. \\ \hline
R.25 & The UI shall have an error diagnostic and feedback system. \\ \hline
R.6 & The hovering altitude shall be adjustable prior to operation (between 0.5 and 2 metres). \\ \hline
R.10 & \textcolor{red}{\sout{There shall be the option to change the predefined flight pattern to a custom option.}} \\ \hline
A.R.1 & \textcolor{red}{\sout{Pre-defined flight path shall follow a polygonal pattern of fixed altitude.}} \\ \hline
A.R.2 & The required drone operational capabilities shall be powered with only one battery. \\ \hline
A.R.3 & \textcolor{red}{\sout{When an obstacle is detected, the drone shall stop and hover until the obstacle is removed or a timeout occurs.}} \\ \hline
A.R.4 & A comprehensive operation manual and user guide shall be provided to the client. \\ \hline
A.R.5 & \textcolor{red}{\sout{The pre-determined flight path shape shall be adjustable in size.}} \\ \hline
A.R.6 & Placement of PCB components shall minimise signal distortion and heating. \\ \hline
A.R.7 & The drone shall have a visual or audible indication during initiation of flight. \\ \hline
A.R.8 & The drone shall alert on the UI in cases of overheating. \\ \hline
A.R.9 & The drone shall have LEDs to show when it is in charging mode. \\ \hline
A.R.10 & The drone shall have indicators to show when it is powering down or operating autonomously. \\ \hline
\end{tabular}
\end{table}

\subsubsection{Additional Requirements - Final (Post-Change List)}

\begin{table}[H]
\centering
\caption{Additional Requirements - Final}
\begin{tabular}{|c|p{11cm}|}
\hline
\textbf{No.} & \textbf{Description} \\ \hline
R.16 & The PCB shall include custom motor drivers. \\ \hline
R.19 & The drone shall be able to fly for a minimum of 3 minutes. \\ \hline
R.28 & The surveillance camera shall stream the live camera feed. \\ \hline
R.26 & The UI shall have a battery level monitoring system for low battery levels. \\ \hline
R.29 & The surveillance camera shall record video for playback. \\ \hline
R.25 & The UI shall have an error diagnostic and feedback system. \\ \hline
R.6 & The hovering altitude shall be adjustable prior to operation (between 0.5 and 2 metres). \\ \hline
A.R.2 & The required drone operational capabilities shall be powered with only one battery. \\ \hline
A.R.4 & A comprehensive operation manual and user guide shall be provided to the client. \\ \hline
A.R.6 & Placement of PCB components shall minimise signal distortion and heating. \\ \hline
A.R.7 & The drone shall have a visual or audible indication during initiation of flight. \\ \hline
A.R.8 & The drone shall alert on the UI in cases of overheating. \\ \hline
A.R.9 & The drone shall have LEDs to show when it is in charging mode. \\ \hline
A.R.10 & The drone shall have indicators to show when it is powering down or operating autonomously. \\ \hline
\end{tabular}
\end{table}

\textbf{Legend:}  
\textcolor{red}{\sout{Removed}} = Requirement removed in final approved version due to scope or redundancy.

%---------------------------------------------------------%
\pagebreak
\subsection{Code}
\label{app:firmware-code}

%---------------------------------------------------------%
\subsubsection{File Structure}
\begin{figure}[H]
    \centering
    
    \caption{File Structure}
\end{figure}

%---------------------------------------------------------%
\subsubsection{sensor.c}

\begin{lstlisting}
//Ref: https://github.com/hibit-dev/mpu6050
//Ref: https://components.espressif.com/components/espressif/mpu6050

#include "i2c.h"
#include "stabiliser.h"
#include "sensors.h"
#include "filter.c"

#define MPU6050_SENSOR_ADDR         0x68
#define MPU6050_WHO_AM_I_REG_ADDR   0x75
#define MPU6050_ACCEL_XOUT_H_ADDR   0x3b 
#define MPU6050_GYRO_XOUT_H_ADDR    0x43
#define MPU6050_PWR_MGMT_1_ADDR     0x6b 
#define MPU6050_GYRO_CONFIG_ADDR    0x1b
#define MPU6050_ACCEL_CONFIG_ADDR   0x1c
#define MPU6050_INT_CFG_ADDR        0x37
#define MPU6050_INT_ENABLE_ADDR     0x38
#define MPU6050_DLPF_ADDR           0x1a
#define MPU6050_H_RESET             0x80
#define MPU6050_SLV4_CTRL_ADDR      0x34
#define MPU6050_MAST_CTRL_ADDR      0x24
#define MPU6050_SMPLRT_DIV_ADDR     0x19

#define GYRO_FULL_SCALE_250_DPS  0x00
#define GYRO_FULL_SCALE_500_DPS  0x08
#define GYRO_FULL_SCALE_1000_DPS 0x10
#define GYRO_FULL_SCALE_2000_DPS 0x18
#define ACC_FULL_SCALE_2G        0x00
#define ACC_FULL_SCALE_4G        0x08
#define ACC_FULL_SCALE_8G        0x10
#define ACC_FULL_SCALE_16G       0x18

#define GYRO_250_SENSITIVITY    (float)((2 * 250.0) / 65536.0)
#define GYRO_500_SENSITIVITY    (float)((2 * 500.0) / 65536.0)
#define GYRO_1000_SENSITIVITY   (float)((2 * 1000.0) / 65536.0)
#define GYRO_2000_SENSITIVITY   (float)((2 * 2000.0) / 65536.0)
#define ACC_2G_SENSITIVITY      (float)((2 * 2) / 65536.0)
#define ACC_4G_SENSITIVITY      (float)((2 * 4) / 65536.0)
#define ACC_8G_SENSITIVITY      (float)((2 * 8) / 65536.0)
#define ACC_16G_SENSITIVITY     (float)((2 * 16) / 65536.0)

#define GYRO_LPF_CUTOFF_FREQ 80
#define ACCE_LPF_CUTOFF_FREQ 30

/* The sensitivity must match the range: */
#define GYRO_SENSITIVITY GYRO_500_SENSITIVITY
#define ACCE_SENSITIVITY ACC_8G_SENSITIVITY
#define GYRO_CONFIG_RANGE GYRO_FULL_SCALE_500_DPS
#define ACCE_CONFIG_RANGE ACC_FULL_SCALE_8G

#define CALIBRATION_SAMPLES 200
#define INT_EN 1
bool use_bias = true;

static const char *TAG = "IMU";

QueueHandle_t acce_queue = NULL;
QueueHandle_t gyro_queue = NULL;
static TaskHandle_t sensor_task_handle = NULL;

static SemaphoreHandle_t mpu6050_data_ready;
static SemaphoreHandle_t sensor_data_ready;

static i2c_master_bus_handle_t bus_handle;
static i2c_master_dev_handle_t dev_handle;
static raw_acce_t raw_acce; 
static raw_gyro_t raw_gyro;
static gyro_t gyro;
static acce_t acce;
static raw_gyro_t gyro_bias = {.x = 0, .y = 0, .z = 0};
static raw_acce_t acce_bias = {.x = 0, .y = 0, .z = 0};
static lpf_data lpf_data_acce[3];
static lpf_data lpf_data_gyro[3];

static bool sensors_init = false;

/* INIT *****************************************************************/
esp_err_t mpu6050_init(i2c_master_bus_handle_t *bus_handle, i2c_master_dev_handle_t *dev_handle) {
    // Intialise the I2C master and device
    i2c_master_init(bus_handle, dev_handle);
    i2c_mpu_device_init(bus_handle, dev_handle);

    ESP_LOGI(TAG, "I2C initialized successfully");
    vTaskDelay(pdMS_TO_TICKS(100)); 
    
    // Reset the registers
    ESP_ERROR_CHECK(mpu6050_register_write_byte(*dev_handle, MPU6050_PWR_MGMT_1_ADDR, MPU6050_H_RESET));
    vTaskDelay(pdMS_TO_TICKS(100)); 
    
    // Set the gyro as the reference
    ESP_ERROR_CHECK(mpu6050_register_write_byte(*dev_handle, MPU6050_PWR_MGMT_1_ADDR, 0x01));

    uint8_t data[2];
    esp_err_t ret = mpu6050_register_read(*dev_handle, MPU6050_WHO_AM_I_REG_ADDR, data, 0x01);
    if (ret != ESP_OK || data[0] != 0x68) return 1;
        
    // Configure the sensor sensitivity
    ESP_ERROR_CHECK(mpu6050_register_write_byte(*dev_handle, MPU6050_ACCEL_CONFIG_ADDR, ACCE_CONFIG_RANGE));
    ESP_ERROR_CHECK(mpu6050_register_write_byte(*dev_handle, MPU6050_GYRO_CONFIG_ADDR, GYRO_CONFIG_RANGE));

    // Enable digital low pass (reduces sample rate from 8kHz to 1kHz)
    ESP_ERROR_CHECK(mpu6050_register_write_byte(*dev_handle, MPU6050_DLPF_ADDR, 0x02)); // 98Hz BW
    ESP_ERROR_CHECK(mpu6050_register_write_byte(*dev_handle, MPU6050_SMPLRT_DIV_ADDR, 0));

    // Enable interrupts
    ESP_ERROR_CHECK(mpu6050_register_write_byte(*dev_handle, MPU6050_INT_ENABLE_ADDR, INT_EN));
    ESP_ERROR_CHECK(mpu6050_register_write_byte(*dev_handle, MPU6050_INT_CFG_ADDR, 0x00));

    // Wake up the IMU
    ESP_ERROR_CHECK(mpu6050_register_write_byte(*dev_handle, MPU6050_PWR_MGMT_1_ADDR, 0x00));
    vTaskDelay(pdMS_TO_TICKS(100)); 

    return ESP_OK;
}

/* De-initialise IMU */
void mpu6050_deinit(i2c_master_bus_handle_t *bus_handle, i2c_master_dev_handle_t *dev_handle) {
    i2c_master_bus_rm_device(*dev_handle);
    i2c_del_master_bus(*bus_handle);
    ESP_LOGI(TAG, "I2C de-initialized successfully");
}

/* MOTION ******************************************************************/
/* Read MPU6050 acceleration */
void mpu6050_read_motion_acce(i2c_master_dev_handle_t *dev_handle, raw_acce_t *raw_acce, acce_t *acce, lpf_data *lpf_data) {
    // Registers (dec):
    // [59-64] Accelerometer

    uint8_t buffer[6];
    esp_err_t ret = mpu6050_register_read(*dev_handle, MPU6050_ACCEL_XOUT_H_ADDR, buffer, sizeof(buffer));

    if (ret != ESP_OK) {
        ESP_LOGE(TAG, "Failed to read from accelerometer");
        return;
    }
    
    raw_acce->x = (((int16_t) buffer[0]) << 8) | buffer[1];
    raw_acce->y = (((int16_t) buffer[2]) << 8) | buffer[3];
    raw_acce->z = (((int16_t) buffer[4]) << 8) | buffer[5];
    
    float x, y, z; 
    x = ((float)(raw_acce->x)) * ACCE_SENSITIVITY;
    y = ((float)(raw_acce->y)) * ACCE_SENSITIVITY;
    z = ((float)(raw_acce->z)) * ACCE_SENSITIVITY;

    acce->x = apply_lpf(&lpf_data[0], x);
    acce->y = apply_lpf(&lpf_data[1], y);
    acce->z = apply_lpf(&lpf_data[2], z);
}

/* Read MPU6050 gyroscope */
void mpu6050_read_motion_gyro(i2c_master_dev_handle_t *dev_handle, raw_gyro_t *raw_gyro, gyro_t *gyro,
                              raw_gyro_t *gyro_bias, lpf_data *lpf_data) {
    // Registers (dec):
    // [67-72] Gyroscope
    uint8_t buffer[6];
    esp_err_t ret = mpu6050_register_read(*dev_handle, MPU6050_GYRO_XOUT_H_ADDR, buffer, sizeof(buffer));
    if (ret != ESP_OK) {
        ESP_LOGE(TAG, "Failed to read from gyro");
        return;
    }

    raw_gyro->x = (((int16_t) buffer[0]) << 8) | buffer[1];
    raw_gyro->y = (((int16_t) buffer[2]) << 8) | buffer[3];
    raw_gyro->z = (((int16_t) buffer[4]) << 8) | buffer[5];
    
    float x, y, z; 
    x = ((float)(raw_gyro->x - gyro_bias->x)) * GYRO_SENSITIVITY;
    y = ((float)(raw_gyro->y - gyro_bias->y)) * GYRO_SENSITIVITY;
    z = ((float)(raw_gyro->z - gyro_bias->z)) * GYRO_SENSITIVITY;

    gyro->x = apply_lpf(&lpf_data[0], x);
    gyro->y = apply_lpf(&lpf_data[1], y);
    gyro->z = apply_lpf(&lpf_data[2], z);
}

void mpu6050_read_motion_raw(i2c_master_dev_handle_t *dev_handle, raw_gyro_t *raw_gyro, raw_acce_t *raw_acce) {
    uint8_t buffer[14];
    mpu6050_register_read(*dev_handle, MPU6050_GYRO_XOUT_H_ADDR, buffer, sizeof(buffer));

    raw_gyro->x = (((int16_t) buffer[0]) << 8) | buffer[1];
    raw_gyro->y = (((int16_t) buffer[2]) << 8) | buffer[3];
    raw_gyro->z = (((int16_t) buffer[4]) << 8) | buffer[5];
    raw_acce->x = (((int16_t) buffer[8]) << 8) | buffer[9];
    raw_acce->y = (((int16_t) buffer[10]) << 8) | buffer[11];
    raw_acce->z = (((int16_t) buffer[12]) << 8) | buffer[13];
}

/* Calibration *************************************************************/
void mpu6050_calibrate(i2c_master_dev_handle_t *dev_handle, raw_gyro_t *raw_gyro, raw_acce_t *raw_acce, raw_gyro_t *gyro_bias, raw_acce_t *acce_bias) {
    uint16_t samples = CALIBRATION_SAMPLES;
    int64_t g_sum_x = 0, g_sum_y = 0, g_sum_z = 0, a_sum_x = 0, a_sum_y = 0, a_sum_z = 0;

    for (int i = 0; i < samples; i++) {
        mpu6050_read_motion_raw(dev_handle, raw_gyro, raw_acce);
        g_sum_x += raw_gyro->x;
        g_sum_y += raw_gyro->y;
        g_sum_z += raw_gyro->z;
        vTaskDelay(pdMS_TO_TICKS(10)); 
    }

    gyro_bias->x = g_sum_x/samples;
    gyro_bias->y = g_sum_y/samples;
    gyro_bias->z = g_sum_z/samples;

    ESP_LOGI(TAG, "Gyro calibrated!");

    ESP_LOGI(TAG, "Gyro Bias: Gx: %.4f Gy: %.4f Gz: %.4f",
        (float)(gyro_bias->x) * GYRO_SENSITIVITY,
        (float)(gyro_bias->y) * GYRO_SENSITIVITY,
        (float)(gyro_bias->z) * GYRO_SENSITIVITY);
}

/**************************************************************/
/* Signal when data is ready from MPU6050 */
void IRAM_ATTR sensorISRHandler(void *arg) {
    // See: FreeRTOS website, xSemaphoreGiveFromISR()
    portBASE_TYPE xHigherPriorityTaskWoken = pdFALSE;
    xSemaphoreGiveFromISR(mpu6050_data_ready, &xHigherPriorityTaskWoken);

    if (xHigherPriorityTaskWoken) {
        portYIELD_FROM_ISR();
    }
}

/* Task *************************************************************/
static void sensor_task(void *arg) {
    // ESP_LOGI(TAG, "Ready to read from mpu6050...");
    while (1) {
        if ((xSemaphoreTake(mpu6050_data_ready, portMAX_DELAY) == pdTRUE)) {
        mpu6050_read_motion_acce(&dev_handle, &raw_acce, &acce, lpf_data_acce);
        xQueueOverwrite(acce_queue, (void *)&acce);

        mpu6050_read_motion_gyro(&dev_handle, &raw_gyro, &gyro, &gyro_bias, lpf_data_gyro);
        xQueueOverwrite(gyro_queue, (void *)&gyro);

        xSemaphoreGive(sensor_data_ready); 
        }
    }
}

void sensor_task_init(void) {
    acce_queue = xQueueCreate(1, sizeof(acce_t));
    gyro_queue = xQueueCreate(1, sizeof(gyro_t));
    mpu6050_data_ready = xSemaphoreCreateBinary();
    sensor_data_ready = xSemaphoreCreateBinary();

    esp_err_t ret = mpu6050_init(&bus_handle, &dev_handle);
    if (ret != ESP_OK) {
        ESP_LOGE(TAG, "Sensor not present or couldn't be read from");
        return;
    }
    vTaskDelay(pdMS_TO_TICKS(100)); 

    if (use_bias) mpu6050_calibrate(&dev_handle, &raw_gyro, &raw_acce, &gyro_bias, &acce_bias);

    for (uint8_t i = 0; i < 3; i++) {
        init_lpf(&lpf_data_acce[i], 1000.0, ACCE_LPF_CUTOFF_FREQ);
        init_lpf(&lpf_data_gyro[i], 1000.0, GYRO_LPF_CUTOFF_FREQ);
    }

    /* Configure interrupt pin */
    gpio_config_t io_conf = {
        .intr_type = GPIO_INTR_POSEDGE, // interrupt of rising edge
        .pin_bit_mask = (1ULL << MPU6050_INT_GPIO_PIN), // bit mask map of the pins for esp
        .mode = GPIO_MODE_INPUT, // set as input mode
        .pull_down_en = 0, // disable pull-down mode
        .pull_up_en = 1, // enable pull-up mode
    };
    
    gpio_config(&io_conf);
    gpio_install_isr_service(0);
    gpio_set_intr_type(MPU6050_INT_GPIO_PIN, GPIO_INTR_POSEDGE);
    gpio_isr_handler_add(MPU6050_INT_GPIO_PIN, sensorISRHandler, (void *)MPU6050_INT_GPIO_PIN);

    ESP_LOGI(TAG, "Sensor interrupt intialised");
    vTaskDelay(pdMS_TO_TICKS(100)); 

    /* Start the task */
    xTaskCreate(sensor_task, "sensor task", 2*1024, NULL, 1, &sensor_task_handle);
    ESP_LOGI(TAG, "Sensor task intialised");
    sensors_init = true; 
}

/**************************************************************/
/* Functions to interface with other tasks */
void waitSensorData() { 
    xSemaphoreTake(sensor_data_ready, portMAX_DELAY);
}

bool sensorsIsInit(void) {
    return sensors_init;
}

void readIMUData(sensor_data_t *sensor_data) {
    xQueuePeek(gyro_queue, (void *)&(sensor_data->gyro), 0);
    xQueuePeek(acce_queue, (void *)&(sensor_data->acce), 0);
}

/**************************************************************/
/* Read from MPU6050 register */
esp_err_t mpu6050_register_read(i2c_master_dev_handle_t dev_handle, uint8_t reg_addr, uint8_t *data, size_t len) {
    return i2c_master_transmit_receive(dev_handle, &reg_addr, 1, data, len, I2C_MASTER_TIMEOUT_MS / portTICK_PERIOD_MS);
}

/* Write to MPU6050 register */
esp_err_t mpu6050_register_write_byte(i2c_master_dev_handle_t dev_handle, uint8_t reg_addr, uint8_t data) {
    uint8_t write_buf[2] = {reg_addr, data};
    return i2c_master_transmit(dev_handle, write_buf, sizeof(write_buf), I2C_MASTER_TIMEOUT_MS / portTICK_PERIOD_MS);
}

/* Initialise MPU device */
void i2c_mpu_device_init(i2c_master_bus_handle_t *bus_handle, i2c_master_dev_handle_t *dev_handle) {
    i2c_device_config_t dev_config = {
        .dev_addr_length = I2C_ADDR_BIT_LEN_7,
        .device_address = MPU6050_SENSOR_ADDR,
        .scl_speed_hz = I2C_MASTER_FREQ_HZ,
    };
    ESP_ERROR_CHECK(i2c_master_bus_add_device(*bus_handle, &dev_config, dev_handle));
}
\end{lstlisting}

%---------------------------------------------------------%
\pagebreak
\subsubsection{filter.c}
\label{app:code-filter}

\begin{lstlisting}
#include "filter.h"
#include <math.h>

/* Initiliase low-pass filter values */
void init_lpf(lpf_data *lpf_data, float fs, float fc) {
    /* Ref: CrazyFlieCore, Filter.c */
    /* Ref: https://www.earlevel.com/main/2003/03/02/the-bilinear-z-transform/ */
    // ohm = tan(pi*Fc/Fs) = K
    // c = K^2 + K/Q + 1, Q = 0.707 (second order butterworth)
    // i.e. 1/Q = 1.414

    float fr = fs/fc; // sampling frequency/cutoff frequency
    float ohm = tanf((float)M_PI/fr);
    float c = 1.0f+2.0f*cosf((float)M_PI/4.0f)*ohm+ohm*ohm; 
    lpf_data->b0 = ohm*ohm/c;
    lpf_data->b1 = 2.0f*lpf_data->b0;
    lpf_data->b2 = lpf_data->b0;
    lpf_data->a1 = 2.0f*(ohm*ohm-1.0f)/c;
    lpf_data->a2 = (1.0f-2.0f*cosf((float)M_PI/4.0f)*ohm+ohm*ohm)/c;
    lpf_data->delayed1 = .0f;
    lpf_data->delayed2 = .0f;
}

/* Apply low-pass filter */
float apply_lpf(lpf_data *lpf_data, float sample) {
    /* Ref: https://en.wikipedia.org/wiki/Digital_biquad_filter */

    //        b0 + b1 z^-1 + b2 z^-2 
    // H(z) = ---------------------- 
    //        1 + a1 z^-1 + a2 z^-2  

    /* Direct form 2 implementation: */
    // w(n) = x(n) - a1 w(n-1) - a2 w(n-2) 
    // y(n) = b0 w(n) + b1 w(n-1) + b3 w(n-2) 
    
    float delayed0 = sample - (lpf_data->delayed1 * lpf_data->a1) - (lpf_data->delayed2 * lpf_data->a2);
    
    if (!isfinite(delayed0)) {
        delayed0 = sample;
    }
        
    float output = (delayed0 * lpf_data->b0) + (lpf_data->delayed1 * lpf_data->b1) + (lpf_data->delayed2 * lpf_data->b2);

    lpf_data->delayed2 = lpf_data->delayed1;
    lpf_data->delayed1 = delayed0;

    return output;
}
\end{lstlisting}
%---------------------------------------------------------%
\pagebreak
\subsubsection{estimator.c}

\begin{lstlisting}
// Ref: CrazyFlieCore, sensorfusion6.c 

#include <math.h>
#include "estimator.h"
#include "sensors.h"
#include "stabiliser.h"

static const char *TAG = "EST";

#define TWO_KP_DEF (2.0f * 0.6f) //(2.0f * 0.4f) // 2 * proportional gain (Kp)
#define TWO_KI_DEF (2.0f * 0.002f) //(2.0f * 0.001f) // 2 * integral gain (Ki)

static const float twoKp = TWO_KP_DEF;    
static const float twoKi = TWO_KI_DEF;    
static float integralFBx = 0.0f;
static float integralFBy = 0.0f;
static float integralFBz = 0.0f;  // integral error terms scaled by Ki

static float grav_x = 0.0f, grav_y = 0.0f, grav_z = 0.0f;
static float qw = 1.0f, qx = 0.0f, qy = 0.0f, qz = 0.0f; 
static float roll = 0.0f, pitch = 0.0f, yaw = 0.0f;
static float velz = 0.0f;

static const float pos_alpha = 0.90f;
static const float vel_alpha = 0.995f;
static const float vel_factor = 1.0f;

static float real_z_acce = 0.0f;
static float base_z = 1.0f; // 1g 
static bool is_acce_calibrated = false;

static bool use_tof = false;

void estimatorComplementary(sensor_data_t *sensor, attitude_t *attitude, float *vel_z, float *pos_z, const uint32_t tick) {
  if (RATE_DO_EXECUTE(ATTITUDE_UPDATE_RATE, tick)) {
    findAttitude(sensor->gyro.x, sensor->gyro.y, sensor->gyro.z, sensor->acce.x, sensor->acce.y, sensor->acce.z, ATTITUDE_UPDATE_DT);
    velocityEstimate(sensor->acce.x, sensor->acce.y, sensor->acce.z, vel_z, ATTITUDE_UPDATE_DT);
    getEulerRPY(attitude); 
  }

  // if (RATE_DO_EXECUTE(ATTITUDE_UPDATE_RATE, tick)) {
  //   positionEstimate(vel_z, pos_z, 0, POS_UPDATE_DT);
  // }
}

/**********************************************************************/
void findAttitude(float gx, float gy, float gz, float ax, float ay, float az, float dt) {
  findQuaterion(gx, gy, gz, ax, ay, az, dt);
  
  // Estimate direction of gravity using quaternion rotation matrix, R(q):
  // [ 1 - 2(qy^2 + qz^2), 2(qx*qy - qw*qz),   2(qx*qz + qw*qy)   ]
  // [ 2(qx*qy + qw*qz),   1 - 2(qx^2 + qz^2), 2(qy*qz - qw*qx)   ]
  // [ 2(qx*qz - qw*qy),   2(qy*qz + qw*qx),   1 - 2(qx^2 + qy^2) ]
  // and point [0, 0, 1].T for gravity (R * p) 
  
  /* Estimate gravity */
  grav_x = 2 * (qx * qz - qw * qy);
  grav_y = 2 * (qw * qx + qy * qz);
  grav_z = qw * qw - qx * qx - qy * qy + qz * qz;

  /* Find gravity from sensors */
  if (!is_acce_calibrated) {
    base_z = (ax * grav_x + ay * grav_y + az * grav_z);
    is_acce_calibrated = true;
  }

  /* Find roll, pitch and yaw */
  if (grav_x>1) grav_x=1;
  if (grav_x<-1) grav_x=-1;

  yaw = atan2f(2*(qx*qy + qw*qz), qw*qw + qx*qx - qy*qy - qz*qz) * 180 / (float)M_PI;

  // These come from rotation matrix for x-axis (Rx) (roll) and rotation matrix for y-axis (Ry) (pitch)
  // Rx(theta) * Ry(psi) * g
  // [     -sin(psi)     ] = -ax => psi = asin(ax)
  // [sin(theta)*cos(psi)] = -ay => cos(psi) = -ay/sin(theta) (1)
  // [cos(psi)*cos(theta)] = -az => from (1): -az = -ay/sin(theta) * cos(theta) -> theta = atan(ay/az)

  pitch = asinf(grav_x) * 180 / (float)M_PI;
  roll = atan2f(grav_y, grav_z) * 180 / (float)M_PI;
}

void velocityEstimate(float ax, float ay, float az, float *vel_z, float dt) {
  real_z_acce = (ax * grav_x + ay * grav_y + az * grav_z) - base_z;
  velz += deadband(real_z_acce, 0.06f) * dt * G;
  velz *= vel_alpha;
  *vel_z = velz;
}

/**********************************************************************/

void positionEstimate(float *vel_z, float *pos_z, float dist, float dt) {
  /* Estimate the position */
  const uint32_t max_sample_age = pdMS_TO_TICKS(50);
  float filtered_z = 0, estimated_z = 0;
  static float prev_estimated_z = 0.0f;

  bool sample_ok = false; // ((xTaskGetTickCount() - tof_data->timestamp) <= max_sample_age);

  if (sample_ok) {
    use_tof = true;
  }

  if (use_tof) {
    filtered_z = (pos_alpha * estimated_z + (1.0f - pos_alpha) * dist);
    estimated_z = filtered_z + (vel_factor * velz * dt);
  } 

  *pos_z = estimated_z;
  *vel_z = (estimated_z - prev_estimated_z) / dt;
  prev_estimated_z = estimated_z;
}

/**********************************************************************/

void getEulerRPY(attitude_t *attitude) {
  attitude->roll = roll; 
  attitude->pitch = pitch;
  attitude->yaw = yaw;
}

void getQuaternion(float *q_w, float *q_x, float *q_y, float *q_z) {
  // Save quaternion 
  *q_w = qw;
  *q_x = qx;
  *q_y = qy;
  *q_z = qz;
}

/**********************************************************************/

void findQuaterion(float gx, float gy, float gz, float ax, float ay, float az, float dt) {
  // gyro: gx, gy, gz
  // acce: ax, ay, az 

  /* Madgwick's implementation of Mayhony's AHRS algorithm (see: http://www.x-io.co.uk/open-source-ahrs-with-x-imu)*/
  // The code is from CrazyFlie

  float recipNorm;
  float halfvx, halfvy, halfvz;
  float halfex, halfey, halfez;
  float qa, qb, qc;

  gx = gx * (float)M_PI / 180 ; // Radians
  gy = gy * (float)M_PI / 180;
  gz = gz * (float)M_PI / 180;

  if(!((ax == 0.0f) && (ay == 0.0f) && (az == 0.0f)))
  {
    // Normalise accelerometer measurement
    recipNorm = invSqrt(ax * ax + ay * ay + az * az);
    ax *= recipNorm;
    ay *= recipNorm;
    az *= recipNorm;

    // Estimated direction of gravity and vector perpendicular to magnetic flux
    halfvx = qx * qz - qw * qy;
    halfvy = qw * qx + qy * qz;
    halfvz = qw * qw - 0.5f + qz * qz;

    // Error is sum of cross product between estimated and measured direction of gravity
    halfex = (ay * halfvz - az * halfvy);
    halfey = (az * halfvx - ax * halfvz);
    halfez = (ax * halfvy - ay * halfvx);

    // Compute and apply integral feedback if enabled
    if(twoKi > 0.0f)
    {
      integralFBx += twoKi * halfex * dt;  // integral error scaled by Ki
      integralFBy += twoKi * halfey * dt;
      integralFBz += twoKi * halfez * dt;
      gx += integralFBx;  // apply integral feedback
      gy += integralFBy;
      gz += integralFBz;
    }
    else
    {
      integralFBx = 0.0f; // prevent integral windup
      integralFBy = 0.0f;
      integralFBz = 0.0f;
    }

    // Apply proportional feedback
    gx += twoKp * halfex;
    gy += twoKp * halfey;
    gz += twoKp * halfez;
  }

  // Integrate rate of change of quaternion
  gx *= (0.5f * dt);   // pre-multiply common factors
  gy *= (0.5f * dt);
  gz *= (0.5f * dt);
  qa = qw;
  qb = qx;
  qc = qy;
  qw += (-qb * gx - qc * gy - qz * gz);
  qx += (qa * gx + qc * gz - qz * gy);
  qy += (qa * gy - qb * gz + qz * gx);
  qz += (qa * gz + qb * gy - qc * gx);

  // Normalise quaternion
  recipNorm = invSqrt(qw * qw + qx * qx + qy * qy + qz * qz);
  qw *= recipNorm;
  qx *= recipNorm;
  qy *= recipNorm;
  qz *= recipNorm;
}

/**********************************************************************/

float invSqrt(float x) {
  return 1.0f/sqrtf(x);
  // float halfx = 0.5f * x;
  // float y = x;
  // long i = *(long*)&y;
  // i = 0x5f3759df - (i>>1);
  // y = *(float*)&i;
  // y = y * (1.5f - (halfx * y * y));
  // return y;
}

float deadband(float value, const float threshold) {
  if (fabsf(value) < threshold)
  {
    value = 0;
  }
  else if (value > 0)
  {
    value -= threshold;
  }
  else if (value < 0)
  {
    value += threshold;
  }
  return value;
}
\end{lstlisting}

%---------------------------------------------------------%
\pagebreak
\subsubsection{controller.c}

\begin{lstlisting}
// Ref: CrazyFlie PID code : ) 

#include "stabiliser.h"
#include "controller.h"
#include "filter.h"
#include "sensors.h"
#include "estimator.h"

static const char *TAG = "PID";
static const bool isManualControl = true;

static attitude_t att_desired = {0};
static attitude_t att_rate_desired = {0};
static attitude_t att_output = {0};
static float actuator_thrust = 0;

PidObject pidRoll;
PidObject pidPitch;
PidObject pidYaw;
PidObject pidRollRate;
PidObject pidPitchRate;
PidObject pidYawRate;
PidObject pidPosX;
PidObject pidPosY;
PidObject pidPosZ;

float thrust_desired = 0; 
float pid_roll = 0, pid_pitch = 0, pid_yaw = 0; 
float pid_is_init = false; 

void controllerInitPID() {
  /* Init all the PID objects */
  pidInit(&pidRollRate, 0, PID_ROLL_RATE_KP, PID_ROLL_RATE_KI, PID_ROLL_RATE_KD,
          ATTITUDE_UPDATE_DT, ATTITUDE_RATE, ATT_RATE_LPF_FC, ATT_RATE_LPF_EN);
  pidInit(&pidPitchRate, 0, PID_PITCH_RATE_KP, PID_PITCH_RATE_KI, PID_PITCH_RATE_KD,
          ATTITUDE_UPDATE_DT, ATTITUDE_RATE, ATT_RATE_LPF_FC, ATT_RATE_LPF_EN);
  pidInit(&pidYawRate, 0, PID_YAW_RATE_KP,   PID_YAW_RATE_KI,   PID_YAW_RATE_KD,
          ATTITUDE_UPDATE_DT, ATTITUDE_RATE, ATT_RATE_LPF_FC, ATT_RATE_LPF_EN);
  
  pidRollRate.int_limit = PID_ROLL_RATE_INT_LIMIT; 
  pidPitchRate.int_limit = PID_PITCH_RATE_INT_LIMIT;
  pidYawRate.int_limit = PID_YAW_RATE_INT_LIMIT;

  pidInit(&pidRoll, 0, PID_ROLL_KP,  PID_ROLL_KI,  PID_ROLL_KD, ATTITUDE_UPDATE_DT,
          ATTITUDE_RATE, ATT_RATE_LPF_FC, ATT_LPF_EN);
  pidInit(&pidPitch, 0, PID_PITCH_KP, PID_PITCH_KI, PID_PITCH_KD, ATTITUDE_UPDATE_DT,
          ATTITUDE_RATE, ATT_RATE_LPF_FC, ATT_LPF_EN);
  pidInit(&pidYaw, 0, PID_YAW_KP,   PID_YAW_KI,   PID_YAW_KD, ATTITUDE_UPDATE_DT,
          ATTITUDE_RATE, ATT_RATE_LPF_FC, ATT_LPF_EN);

  pidRoll.int_limit = PID_ROLL_INT_LIMIT; 
  pidPitch.int_limit = PID_PITCH_INT_LIMIT;
  pidYaw.int_limit = PID_YAW_INT_LIMIT;

  //To-Do: Add position controller

  pid_is_init = true;
}

void controllerPID(sensor_data_t *sensor, state_t *state, setpoint_t *setpoint, control_t *control, const uint32_t tick) {
  if (RATE_DO_EXECUTE(ATTITUDE_RATE, tick)) {
      att_desired.yaw += setpoint->attitudeRate.yaw * ATTITUDE_UPDATE_DT;
      att_desired.yaw = angleLimit(att_desired.yaw); 
  }

  /* Position controller */
  // This gets the thrust from the z velocity (outer-outer loop)
  // To-do: consider x, y tuning
  // (which updates the desired attitude from something other than zero (stable hover))
  // if (RATE_DO_EXECUTE(POSITION_RATE, tick)) {
  //   positionController(&actuator_thrust, &att_desired, setpoint, state);
  // }

  if (RATE_DO_EXECUTE(ATTITUDE_RATE, tick)) {
    actuator_thrust = setpoint->thrust; // Use this for now 
    att_desired.roll = setpoint->attitude.roll;
    att_desired.pitch = setpoint->attitude.pitch; 

    /* Attitude Control */
    /* PID for attitude */
    // This gets the attitude rate from the attitude (outer loop)
    pidRoll.desired = att_desired.roll;
    att_rate_desired.roll = pidUpdate(&pidRoll, state->attitude.roll, true); 

    pidPitch.desired = att_desired.pitch;
    att_rate_desired.pitch = pidUpdate(&pidPitch, state->attitude.pitch, true); 

    float yaw_error;
    yaw_error = setpoint->attitude.yaw - state->attitude.yaw;
    yaw_error = angleLimit(yaw_error);
    pidYaw.error = yaw_error;
    att_rate_desired.yaw = pidUpdate(&pidYaw, state->attitude.yaw, false);
    
    /* Attitude Rate Control */
    // From the attitude rate get an output to the motor! (inner loop)
    pidRollRate.desired = att_rate_desired.roll;
    att_output.roll = pidUpdate(&pidRollRate, sensor->gyro.x, true);
    pidPitchRate.desired = att_rate_desired.pitch;
    att_output.pitch = pidUpdate(&pidPitchRate, sensor->gyro.y, true);
    pidYawRate.desired = att_rate_desired.yaw;
    att_output.yaw = pidUpdate(&pidYawRate, sensor->gyro.z, true);

    control->roll = saturateSignedInt16(att_output.roll);
    control->pitch = saturateSignedInt16(att_output.pitch);
    control->yaw = saturateSignedInt16(att_output.yaw);

    if (isManualControl) {
      control->thrust = scaleThrust(actuator_thrust);
      // control->roll = scaleAngle90(setpoint->attitude.roll);
      // control->pitch = scaleAngle90(setpoint->attitude.pitch); 
      // control->yaw = scaleAngle180(att_desired.yaw); 
    } else {
      control->thrust = actuator_thrust;
    } 

    if (RATE_DO_EXECUTE(LOG_RATE, tick)) {
      ESP_LOGI(TAG, "tick=%lu", (unsigned long)tick);
      ESP_LOGI(TAG, "att_des: [roll=%.2f pitch=%.2f yaw=%.2f] thrust=%.2f",
        att_desired.roll, att_desired.pitch, att_desired.yaw, actuator_thrust);
      ESP_LOGI(TAG, "att_rate_des: [roll=%.2f pitch=%.2f yaw=%.2f]",
       att_rate_desired.roll, att_rate_desired.pitch, att_rate_desired.yaw);
      ESP_LOGI(TAG, "thrust: [act=%.2f out=%.2f]",
      actuator_thrust, control->thrust);
    }
  }
}

/******************************************************************/

void positionController(float *thrust, attitude_t *att_desired, setpoint_t *setpoint, state_t *state) {
  // Not finished
  thrust_desired = setpoint->thrust;

  float cosyaw = cosf(state->attitude.yaw * (float)M_PI / 180.0f);
  float sinyaw = sinf(state->attitude.yaw * (float)M_PI / 180.0f);
  float bodyvx = setpoint->vx;
  float bodyvy = setpoint->vy;
  setpoint->vx = bodyvx * cosyaw - bodyvy * sinyaw;
  setpoint->vy = bodyvy * cosyaw + bodyvx * sinyaw;

  pidPosZ.desired = setpoint->z;
  setpoint->vz = pidUpdate(&pidPosZ, state->z, true);
}

/******************************************************************/

// From CrazyFlie core, PID.C
void pidInit(PidObject* pid, float desired, float kp, float ki, float kd, float dt, float fs, float fc, bool en_filter) {
  pid->desired = desired;
  pid->error = 0;
  pid->prev_error = 0;
  pid->integ = 0;
  pid->deriv = 0;
  pid->kp = kp;
  pid->ki = ki;
  pid->kd = kd;
  pid->int_limit = 5000.0;
  pid->out_limit = 0.0;
  pid->dt = dt;
  pid->d_filter_en = en_filter;

  if (pid->d_filter_en) {
    init_lpf(&pid->d_filter, fs, fc);
  }
}

float pidUpdate(PidObject* pid, float measured, bool update_error) {
  float output = 0.0f;

  if (update_error) {
    pid->error = pid->desired - measured;
  }

  /* Proportional */
  pid->out_p = pid->kp * pid->error;
  output += pid->out_p;

  /* Derivative */
  float deriv = (pid->error - pid->prev_error) / pid->dt;
  if (pid->d_filter_en) {
    pid->deriv = apply_lpf(&pid->d_filter, deriv);
  } else {
    pid->deriv = deriv;
  }

  if (isnan(pid->deriv)) {
    pid->deriv = 0;
  }
  
  pid->out_d = pid->kd * pid->deriv;
  output += pid->out_d;

  /* Integral */
  pid->integ += pid->error * pid->dt;

  // Constrain the integral (unless the int_limit is zero)
  if(pid->int_limit != 0) {
    pid->integ = constrain(pid->integ, -pid->int_limit, pid->int_limit);
  }

  pid->out_i = pid->ki * pid->integ;
  output += pid->out_i;

  // Constrain the total PID output (unless the out_limit is zero)
  if(pid->out_limit != 0) {
    output = constrain(output, -pid->out_limit, pid->out_limit);
  }

  pid->prev_error = pid->error;

  return output;
}

/******************************************************************/
float scaleThrust(float actuator_thrust) {
    // for actuator_thrust between 0-100
    if (actuator_thrust < 0.0f) actuator_thrust = 0.0f;
    if (actuator_thrust > 100.0f) actuator_thrust = 100.0f;
    // Scale 0-100 -> THRUST_MIN-THRUST_MAX
    return (actuator_thrust / 100.0f) * (float)(THRUST_MAX - THRUST_MIN) + THRUST_MIN;
}

float scaleAngle90(float setpoint) {
    return (setpoint/90.0f) * (float)(INT16_MAX);
}

float scaleAngle180(float setpoint) {
    return (setpoint/180.0f) * (float)(INT16_MAX);
}

// Some helpers from CrazyFlie : )
float angleLimit(float angle) {
  float result = angle;

  while (result > 180.0f) {
    result -= 360.0f;
  }

  while (result < -180.0f) {
    result += 360.0f;
  }

  return result;
}

int16_t saturateSignedInt16(float in)
{
  if (in > INT16_MAX)
    return INT16_MAX;
  else if (in < -INT16_MAX)
    return -INT16_MAX;
  else
    return (int16_t)in;
}

float constrain(float value, const float minVal, const float maxVal)
{
  return fminf(maxVal, fmaxf(minVal,value));
}
\end{lstlisting}

%---------------------------------------------------------%
\pagebreak
\subsubsection{stabiliser.c}

\begin{lstlisting}
#include "stabiliser.h"
#include "websocket.h"
#include "sensors.h"
#include "estimator.h"
#include "controller.h"
#include "motors.h"

#define TESTING false
#define YAW_OFF false

static const char *TAG = "STAB";

#define TIMEOUT_STABILIZE pdMS_TO_TICKS(1000)

static TaskHandle_t stabiliser_task_handle = NULL;

static QueueHandle_t socket_data_queue = NULL;
static QueueHandle_t setpoint_queue = NULL;

static uint32_t lastWakeTime;
static const TickType_t xFrequency = 1;

static state_t state = {0};
static setpoint_t setpoint = {0};
static control_t control = {0};
static sensor_data_t sensor_data = {0};
static socket_data_t socket_data = {0};
static tof_data_t tof_data = {0}; //(?)

const static control_t control_reset = {0};

static bool websocket_disconnect = false;

/**************************************************************/

static void stabiliser_task(void* param) {
  uint32_t tick; 

  if (!sensorsIsInit() && !websocket_is_init()) {
    vTaskDelay(portMAX_DELAY);
  }
  ESP_LOGI(TAG, "Ready to fly!");

  lastWakeTime = xTaskGetTickCount(); // not using this right now but may use later
  tick = 1;

  while(1) {
    waitSensorData();
    readIMUData(&sensor_data);
    
    /* Get state estimate */
    // Also position estimate (to-do)
    // wait_for_vlx_data();
    estimatorComplementary(&sensor_data, &state.attitude, &state.vz, &state.z, tick);

    /* Update display data */
    sendDisplaySocket();
    
    /* Get set point */
    getSetpoint(&setpoint); 
    stabiliserLog(tick);

    /* PID controller */
    controllerPID(&sensor_data, &state, &setpoint, &control, tick);

    /******* Testing ********/ 
    control.yaw = 0;
    
    /* Send control points to motors */
    if (setpoint.enable && !websocket_disconnect) {
      powerDistribution(&control); 
    } else {
      powerDistribution(&control_reset); 
    }
    
    // Update tick
    tick++;
    vTaskDelayUntil(&lastWakeTime, xFrequency);
  }
}

bool stabiliserTest(void) {
  bool pass = true;
  pass &= powerDistributionTest(); 
  return pass;
}

/**************************************************************/

void getSetpoint(setpoint_t *setpoint) {
  uint32_t now = xTaskGetTickCount();

  if(xQueuePeek(setpoint_queue, (void *)setpoint, 0) == pdTRUE) {
    // setpoint->attitude.roll = 0;
    // setpoint->attitude.pitch = 0;
    // setpoint->attitudeRate.yaw = 0;

    if (((now - setpoint->timestamp) > TIMEOUT_STABILIZE) && !websocket_disconnect && !TESTING) {
      // To-do: might need to change how the timeout works
      setpoint->enable = false;
      websocket_disconnect = true; 
      ESP_LOGE(TAG, "Websocket timestamp too old, disabling motors");
      return;
    }  
  }

  websocket_disconnect = false; 
}

void setSetpoint(setpoint_t *setpoint) {
  xQueueOverwrite(setpoint_queue, setpoint);
}

void sendDisplaySocket() {
  socket_data.attitude = state.attitude;
  socket_data.z = state.z;
  socket_data.control = control;
  xQueueOverwrite(socket_data_queue, (void *)&socket_data);
}

void readSocketData(sensor_data_t *sensor, socket_data_t *socket_data) {
  xQueuePeek(socket_data_queue, (void *)socket_data, 0);
}

/**************************************************************/

void stabiliserLog(const uint32_t tick) {
  if (RATE_DO_EXECUTE(LOG_RATE, tick)) {
      ESP_LOGI(TAG, "tick=%lu", (unsigned long)tick);
      ESP_LOGI(TAG, "sensor: gyro[%.2f %.2f %.2f] acce[%.2f %.2f %.2f]",
        sensor_data.gyro.x, sensor_data.gyro.y, sensor_data.gyro.z,
        sensor_data.acce.x, sensor_data.acce.y, sensor_data.acce.z);
      ESP_LOGI(TAG, "state: att[roll=%.2f pitch=%.2f yaw=%.2f] vz=%.2f z=%.2f",
        state.attitude.roll, state.attitude.pitch, state.attitude.yaw,
        state.vz, state.z);
      ESP_LOGI(TAG, "setpoint: att[roll=%.2f pitch=%.2f yaw=%.2f] enable %d "
                    "attRate[roll=%.2f pitch=%.2f yaw=%.2f] thrust=%.2f",
        setpoint.attitude.roll, setpoint.attitude.pitch, setpoint.attitude.yaw, setpoint.enable,
        setpoint.attitudeRate.roll, setpoint.attitudeRate.pitch, setpoint.attitudeRate.yaw, setpoint.thrust);
      ESP_LOGI(TAG, "control: roll=%d pitch=%d yaw=%d thrust=%.2f",
        control.roll, control.pitch, control.yaw, control.thrust);
  }
}

void stabiliserTaskInit(void) {
    socket_data_queue = xQueueCreate(1, sizeof(socket_data_t));
    setpoint_queue = xQueueCreate(1, sizeof(setpoint_t));

    /* Init */
    motorsInit();
    PWMTimerInit();
    ESP_LOGI(TAG, "Motor GPIO intialised");

    controllerInitPID();
    ESP_LOGI(TAG, "PID controller intialised");

    /* Tests */
    if (!stabiliserTest()) {
      ESP_LOGE(TAG, "Stabiliser tests failed");
    } else {
      ESP_LOGI(TAG, "Stabiliser tests passed");
    }

    /* Task */
    xTaskCreate(stabiliser_task, "stabiliser task", 3*1024, NULL, 5, &stabiliser_task_handle);
    ESP_LOGI(TAG, "Stabiliser task intialised");
}

\end{lstlisting}

%---------------------------------------------------------%
\pagebreak
\subsubsection{motors.c}

\begin{lstlisting}
// From CrazyFlie core, power_distribution_stock.c
// ESP Driver, motors.c

#include "driver/ledc.h"
#include "motors.h"
#include "stabiliser.h"

static bool isInit = false;
static bool isTimerInit = false;

uint32_t motor_ratios[] = {0, 0, 0, 0};
const uint32_t MOTORS[] = {MOTOR_M1, MOTOR_M2, MOTOR_M3, MOTOR_M4};

static uint32_t idleThrust = DEFAULT_IDLE_THRUST;

static struct {
  uint32_t m1;
  uint32_t m2;
  uint32_t m3;
  uint32_t m4;
} motorPower;

ledc_channel_config_t motors_channel[NBR_OF_MOTORS] = {
    {
        .channel = MOT_PWM_CH1,
        .duty = 0,
        .gpio_num = MOTOR1_GPIO,
        .speed_mode = LEDC_LOW_SPEED_MODE,
        .timer_sel = LEDC_TIMER_0
    },
    {
        .channel = MOT_PWM_CH2,
        .duty = 0,
        .gpio_num = MOTOR2_GPIO,
        .speed_mode = LEDC_LOW_SPEED_MODE,
        .timer_sel = LEDC_TIMER_0
    },
    {
        .channel = MOT_PWM_CH3,
        .duty = 0,
        .gpio_num = MOTOR3_GPIO,
        .speed_mode = LEDC_LOW_SPEED_MODE,
        .timer_sel = LEDC_TIMER_0
    },
    {
        .channel = MOT_PWM_CH4,
        .duty = 0,
        .gpio_num = MOTOR4_GPIO,
        .speed_mode = LEDC_LOW_SPEED_MODE,
        .timer_sel = LEDC_TIMER_0
    },
};

bool powerDistributionTest(void) {
  bool pass = true;
  pass &= motorsTest();
  return pass;
}

void powerDistribution(const control_t *control) {
    int16_t r = control->roll / 2.0f;
    int16_t p = control->pitch / 2.0f;

    motorPower.m1 = limitUint16(control->thrust - r + p + control->yaw);
    motorPower.m2 = limitUint16(control->thrust - r - p - control->yaw);
    motorPower.m3 = limitUint16(control->thrust + r - p + control->yaw);
    motorPower.m4 = limitUint16(control->thrust + r + p - control->yaw);

    // motorPower.m1 = limitUint16(control->thrust);
    // motorPower.m2 = limitUint16(control->thrust);
    // motorPower.m3 = limitUint16(control->thrust);
    // motorPower.m4 = limitUint16(control->thrust);

    if (motorPower.m1 < idleThrust) {
      motorPower.m1 = idleThrust;
    }
    if (motorPower.m2 < idleThrust) {
      motorPower.m2 = idleThrust;
    }
    if (motorPower.m3 < idleThrust) {
      motorPower.m3 = idleThrust;
    }
    if (motorPower.m4 < idleThrust) {
      motorPower.m4 = idleThrust;
    }

    motorsSetRatio(MOTOR_M1, motorPower.m1);
    motorsSetRatio(MOTOR_M2, motorPower.m2);
    motorsSetRatio(MOTOR_M3, motorPower.m3);
    motorsSetRatio(MOTOR_M4, motorPower.m4);
}

/**********************************************************************/

// thrust mapped for 65536 <==> 60 grams
void motorsSetRatio(uint32_t id, uint16_t ithrust) {
    if (isInit) {
        uint16_t ratio;
        ratio = ithrust;
        ledc_set_duty(motors_channel[id].speed_mode, motors_channel[id].channel, (uint32_t)motorsConv16ToBits(ratio));
        ledc_update_duty(motors_channel[id].speed_mode, motors_channel[id].channel);
        motor_ratios[id] = ratio;
    }
}

bool motorsTest(void) {
    int i;
    for (i = 0; i < sizeof(MOTORS) / sizeof(*MOTORS); i++) {
          motorsSetRatio(MOTORS[i], MOTORS_TEST_RATIO);
          vTaskDelay(pdMS_TO_TICKS(MOTORS_TEST_ON_TIME_MS));
          motorsSetRatio(MOTORS[i], 0);
          vTaskDelay(pdMS_TO_TICKS(MOTORS_TEST_DELAY_TIME_MS));
    }
    return isInit;
}

/**********************************************************************/

void motorsInit(void) {
    int i;
    if (isInit) {
        return;
    }
    if (PWMTimerInit() != true) {
        return;
    }
    for (i = 0; i < NBR_OF_MOTORS; i++) {
        ledc_channel_config(&motors_channel[i]);
    }
    isInit = true;
}

void motorsDeInit(void) {
    for (int i = 0; i < NBR_OF_MOTORS; i++) {
        ledc_stop(motors_channel[i].speed_mode, motors_channel[i].channel, 0);
    }
}

bool PWMTimerInit(void) {
    if (isTimerInit) {
        return true;
    }

    ledc_timer_config_t ledc_timer = {
        .duty_resolution = MOTORS_PWM_BITS, // resolution of PWM duty
        .freq_hz = 15000,	// frequency of PWM signal
        .speed_mode = LEDC_LOW_SPEED_MODE, // timer mode
        .timer_num = LEDC_TIMER_0, // timer index
    };

    // Set configuration of timer0 for high speed channels
    if (ledc_timer_config(&ledc_timer) == ESP_OK) {
        isTimerInit = true;
        return true;
    }

    return false;
}

/**********************************************************************/

uint16_t limitUint16(int32_t value) {
  if(value > UINT16_MAX) {
    value = UINT16_MAX;
  } else if(value < 0) {
    value = 0;
  }
  return (uint16_t)value;
}

uint16_t motorsConvBitsTo16(uint16_t bits) {
    return ((bits) << (16 - MOTORS_PWM_BITS));
}

uint16_t motorsConv16ToBits(uint16_t bits) {
    return ((bits) >> (16 - MOTORS_PWM_BITS) & ((1 << MOTORS_PWM_BITS) - 1));
}
\end{lstlisting}

%---------------------------------------------------------%
\pagebreak
\subsubsection{websocket.c}

\begin{lstlisting}

// Ref: ESP-IDF v5.5 "ws_echo_server"
// Ref: https://esp32tutorials.com/esp32-esp-idf-websocket-web-server/

#include "sensors.h"
#include "stabiliser.h"
#include "websocket.h"

static const char *TAG = "WEB";

static httpd_handle_t server = NULL;
static sensor_data_t sensor_data = {0};
static socket_data_t display = {0};
static bool websocket_init = false;

void get_imu_data(char *data, uint8_t len) {
    readIMUData(&sensor_data);
    snprintf(data, len, "imu%06.2f%06.2f%06.2f%06.2f%06.2f%06.2f",
             sensor_data.acce.x, sensor_data.acce.y, sensor_data.acce.z,
             sensor_data.gyro.x, sensor_data.gyro.y, sensor_data.gyro.z);
}

void get_display(char *data, uint8_t len) {
    readSocketData(&sensor_data, &display);
    snprintf(data, len, "rpy%06.2f%06.2f%06.2f%06.2f%06.2f%06.2f%06.2f%06.2f",
             display.attitude.roll, display.attitude.pitch, display.attitude.yaw, display.z,
             (float)display.control.roll, (float)display.control.pitch, (float)display.control.yaw, display.control.thrust);
}

void send_setpoint(char *data, uint8_t len) {
    if (len < sizeof(setpoint_t)) return;
    setpoint_t sp;
    memcpy(&sp, data, sizeof(setpoint_t));
    sp.timestamp = xTaskGetTickCount();
    setSetpoint(&sp);
}

/**************************************************************/

void async_send(void *arg) {
    struct async_send_arg *resp_arg = arg;
    httpd_handle_t hd = resp_arg->hd;
    int fd = resp_arg->fd;

    data_read_function funct = resp_arg->funct; 
    char data[255] = {0};
    funct(data, sizeof(data)-1); // pass the correct data function

    httpd_ws_frame_t ws_pkt;
    memset(&ws_pkt, 0, sizeof(httpd_ws_frame_t));
    ws_pkt.payload = (uint8_t*)data;
    ws_pkt.len = strlen(data);
    ws_pkt.type = HTTPD_WS_TYPE_TEXT;

    httpd_ws_send_frame_async(hd, fd, &ws_pkt);
    free(resp_arg);
}

esp_err_t trigger_async_send(httpd_handle_t handle, httpd_req_t *req, data_read_function funct) {
    struct async_send_arg *resp_arg = malloc(sizeof(struct async_send_arg));
    
    if (resp_arg == NULL) {
        return ESP_ERR_NO_MEM;
    }
    
    resp_arg->hd = req->handle;
    resp_arg->fd = httpd_req_to_sockfd(req);
    resp_arg->funct = funct; 
    esp_err_t ret = httpd_queue_work(handle, async_send, resp_arg);
    
    if (ret != ESP_OK) {
        free(resp_arg);
    }
    
    return ret;
}

/**************************************************************/
/* Handle messages being recieved from clients */
esp_err_t handle_ws_req(httpd_req_t *req)
{
    if (req->method == HTTP_GET) {
        ESP_LOGI(TAG, "Handshake done, the new connection was opened");
        return ESP_OK;
    }

    httpd_ws_frame_t ws_pkt;
    uint8_t *buf = NULL;
    memset(&ws_pkt, 0, sizeof(httpd_ws_frame_t));
    ws_pkt.type = HTTPD_WS_TYPE_TEXT;
    
    // Set max_len = 0 to get the frame len
    esp_err_t ret = httpd_ws_recv_frame(req, &ws_pkt, 0);
    if (ret != ESP_OK) {
        ESP_LOGE(TAG, "httpd_ws_recv_frame failed to get frame len with %d", ret);
        return ret;
    }
    
    // ESP_LOGI(TAG, "frame len is %d", ws_pkt.len);
    if (ws_pkt.len) {
        // ws_pkt.len + 1 is for NULL termination as we are expecting a string 
        buf = calloc(1, ws_pkt.len + 1);
        if (buf == NULL) {
            ESP_LOGE(TAG, "Failed to calloc memory for buf");
            return ESP_ERR_NO_MEM;
        }
        ws_pkt.payload = buf;
        // Set max_len = ws_pkt.len to get the frame payload 
        ret = httpd_ws_recv_frame(req, &ws_pkt, ws_pkt.len);
        if (ret != ESP_OK) {
            ESP_LOGE(TAG, "httpd_ws_recv_frame failed with %d", ret);
            free(buf);
            return ret;
        }
        // ESP_LOGI(TAG, "Got packet with message: %s", ws_pkt.payload);
    }
    // ESP_LOGI(TAG, "Packet type: %d", ws_pkt.type);

    /* Handle messages */
    if (ws_pkt.type == HTTPD_WS_TYPE_TEXT) {
        if (strcmp((char*)ws_pkt.payload, "request imu") == 0) {
            free(buf);
            return trigger_async_send(req->handle, req, get_imu_data);
        } else if (strcmp((char*)ws_pkt.payload, "request rpy") == 0) {
            free(buf);
            ret = trigger_async_send(req->handle, req, get_display);
            return (trigger_async_send(req->handle, req, get_imu_data) || ret); // changes
        }
    }

    if (ws_pkt.type == HTTPD_WS_TYPE_BINARY) {
        if (strncmp((char*)ws_pkt.payload, "set", 3) == 0) {
            // ESP_LOGI(TAG, "Setpoint received");
            if (ws_pkt.len >= 3 + sizeof(setpoint_t)) {
                setpoint_t sp;
                memcpy(&sp, ws_pkt.payload + 3, sizeof(setpoint_t));
                send_setpoint((char*)&sp, sizeof(setpoint_t));
            } 
        }
    }
    
    ret = httpd_ws_send_frame(req, &ws_pkt);
    if (ret != ESP_OK) {
        ESP_LOGE(TAG, "httpd_ws_send_frame failed with %d", ret);
    }
    free(buf);

    return ret;
}

/**************************************************************/

const httpd_uri_t ws = {
        .uri        = "/ws",
        .method     = HTTP_GET,
        .handler    = handle_ws_req,
        .user_ctx   = NULL,
        .is_websocket = true
};

httpd_handle_t start_webserver(void) {
    httpd_handle_t server = NULL;
    httpd_config_t config = HTTPD_DEFAULT_CONFIG();
    
    ESP_LOGI(TAG, "Starting server on port: '%d'", config.server_port);
    if (httpd_start(&server, &config) == ESP_OK) {
        ESP_LOGI(TAG, "Registering URI handlers");
        httpd_register_uri_handler(server, &ws);
        return server;
    }
    ESP_LOGI(TAG, "Error starting server!");
    return NULL;
}

void websocket_task_init(void) {
    ESP_ERROR_CHECK(nvs_flash_init());
    ESP_ERROR_CHECK(esp_netif_init());
    ESP_ERROR_CHECK(esp_event_loop_create_default());
    esp_err_t ret = example_connect();

    if (ret != ESP_OK) {
        ESP_LOGE(TAG, "Server failed to connect");
        return; 
    }

    server = start_webserver();

    websocket_init = true;
}

bool websocket_is_init() {
    return websocket_init;
}
\end{lstlisting}

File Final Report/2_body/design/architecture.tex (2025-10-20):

\subsection{Requirements}
\label{sec:ranked-requirements}

Project requirements define the measurable outcomes of the design process and establish a shared understanding between the client and the development team. Each requirement must be technically sound, verifiable, and achievable within the defined project constraints. 

Requirements were derived from the project brief, client discussions, and technical analysis. Constraints and assumptions were first identified, followed by a prioritisation process based on technical criticality, safety relevance, and feasibility. A detailed record of this process is available in the \textit{Requirements Report}. The ranked requirements are given below in \ref{tab:ranked-req}. The constraints for the requirements can be found in Appendix~\ref{app:constraints}.

\begin{table}[H]
\centering
\caption{Ranked Requirements}
\label{tab:ranked-req}
\begin{tabular}{|>{\centering\arraybackslash}p{0.05\textwidth} | >{\centering\arraybackslash}p{0.07\textwidth} | p{0.65\textwidth} | >{\centering\arraybackslash}p{0.1\textwidth}|}
\hline
\rowcolor{gray!15}
\textbf{Rank} & \textbf{No.} & \textbf{Requirement} & \textbf{Constr.} \\
\hline
1 & R.2  & The drone shall be capable of hovering and flying. & C.1 \\
\hline
2 & R.30 & The drone must power off after 30~s of disconnection. & C.6 \\
\hline
3 & R.1  & The drone shall operate in an indoor area. & C.3 \\
\hline
4 & R.17 & The drone shall utilise shrouded propellers or propeller guards. & C.6 \\
\hline
5 & R.3  & The drone shall navigate without the use of \gls{gps}. & C.3 \\
\hline
6 & R.4  & The drone shall maintain a set hovering altitude during autonomous
surveillance. & C.3 \\
\hline
7 & R.14 & A manual override system shall be available to the user. & C.2, C.7 \\
\hline
8 & R.27 & The drone shall autonomously land safely when battery levels are low. & C.
3 \\
\hline
9 & R.24 & Any third-party software used for control must be open-source and freely available. & C.2 \\
\hline
10 & R.23 & The drone design shall remain within a budget of \textdollar350.00. & C.4 \\
\hline
11 & R.20 & The drone shall be capable of flight stabilisation. & C.2, C.7 \\
\hline
12 & R.5  & The drone shall maintain a default altitude between 1.2--1.3m during operation. & C.2 \\
\hline
13 & R.18 & Power shall be supplied by one 1S or 2S \gls{lipo} battery (<800~mAh). & C.6 \\
\hline
14 & R.15 & The flight controller shall use a custom PCB integrating sensors and power distribution. & C.2 \\
\hline
15 & R.21 & The drone shall maintain stability under wind disturbances. & C.2, C.7 \\
\hline
\end{tabular}
\end{table}

The system must operate reliably in confined indoor environments, maintain stable and controllable flight without GPS, and integrate safety mechanisms that protect both users and equipment. Core requirements prioritise flight stability, communication reliability, and compliance with weight, power, and cost limits. Lower-priority requirements cover enhancements such as diagnostics, video capability, and improved user interface feedback.

There are also several lower-priority requirements that are not essential to meeting the primary project goals but remain background considerations. These features may still be implemented if they can be added with minimal time or resource overhead. The additional requirements are given in Appendix~\ref{app:additional_req}.

The ranked requirements form the foundation for architectural, hardware, and software decisions presented in the following sections.

%----------------------------------------------------------------%
\subsection{Design Architecture}

The design architecture defines how major subsystems interact to meet functional, safety, and performance requirements. It establishes clear boundaries between sensing, control, communication, and actuation components, ensuring reliable operation and outlining the integration of these components with each other.

While the desired behaviour of the system establishes its requirements, along with additional factors such as safety considerations and other constraints that influence the final design, the system architecture represents the high-level realisation of these requirements. It defines the main function elements of the system and the interfaces between them. Based on this architecture, specific design components are then selected to best implement the intended functionality.

\begin{figure}[H]
    \centering
    \captionsetup{justification=centering, margin=1cm}
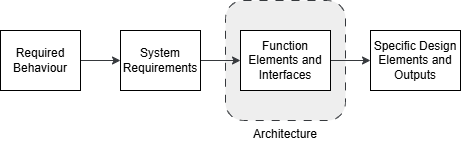
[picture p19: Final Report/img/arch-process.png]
    
    \caption{System Architecture Process}
    \label{fig:arch-process}
\end{figure}

%-------------------------------------------------------------%
\subsubsection{Overall Architecture}

The overall system architecture, shown in Fig.~\ref{fig:block-overall}, is divided into three main layers: the User–Web Interface, the Web–Firmware Interface, and the Firmware–Hardware Interface. These layers communicate through well-defined protocols to ensure reliable and modular operation.

\begin{figure}[H]
    \centering
    \captionsetup{justification=centering, margin=1cm}
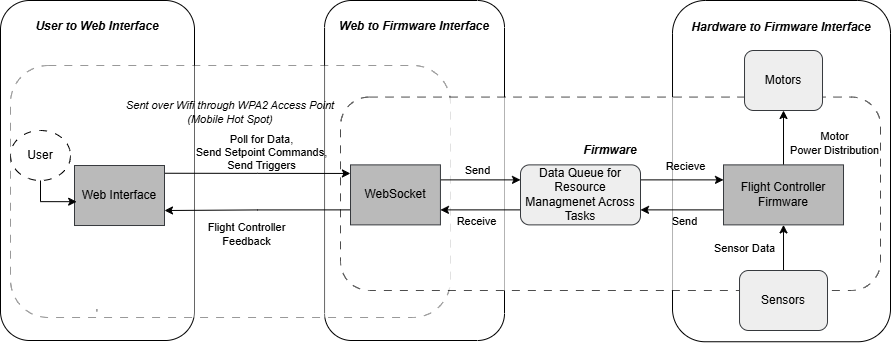
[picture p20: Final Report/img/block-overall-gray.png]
    
    \caption{Overall System Architecture with Hardware and Firmware Interfaces}
    \label{fig:block-overall}
\end{figure}

\textbf{User to Web Interface}: The operator controls the drone and monitors system feedback via a web interface supporting both manual and autonomous flight. Real-time telemetry, sensor feedback, and emergency motor shutdown are provided over a WPA2-secured Wi-Fi connection.

\textbf{Web to Firmware Interface}: A persistent WebSocket link connects the web interface and the flight controller. Three message types are supported: (i) \textit{data requests} for sensor feedback, (ii) \textit{setpoint commands} for control updates, and (iii) \textit{control triggers} for testing or initiating sequences. The WebSocket and control processes run as independent \gls{rtos} tasks, communicating via thread-safe queues to prevent race conditions.

\textbf{Firmware to Hardware Interface}: The flight controller directly interfaces with onboard sensors and motor drivers. Sensor data is continuously processed to generate thrust commands that maintain stable flight. The control loop responds in real time to user or autonomous inputs, ensuring stable hover and smooth manoeuvres.

The design philosophy for the indoor \gls{uav} is founded on the principles of simplicity, modularity, and maintainability, ensuring a system that is functional, safe, and adaptable within its operating environment. Simplicity reduces unnecessary complexity and potential failure points, modularity enables independent development and integration of subsystems, and maintainability supports long-term reliability through ease of repair and clear documentation. These principles are reinforced by high-level design considerations - functionality, safety, cost-effectiveness, sustainability, reliability, and usability - ensuring that the final system achieves stable, efficient, and safe autonomous flight in confined indoor environments.

The following sections describe the hardware and firmware architectures in further detail.

%-------------------------------------------------------------%
\subsubsection{Hardware Architecture}

The hardware architecture integrates sensing, control, communication, and power management into a single lightweight \gls{pcb} mounted on a 3D printed frame. Fig.~\ref{fig:block-hardware} illustrates the main components and their interconnections. 

\begin{figure}[H]
    \centering
    \captionsetup{justification=centering, margin=1cm}
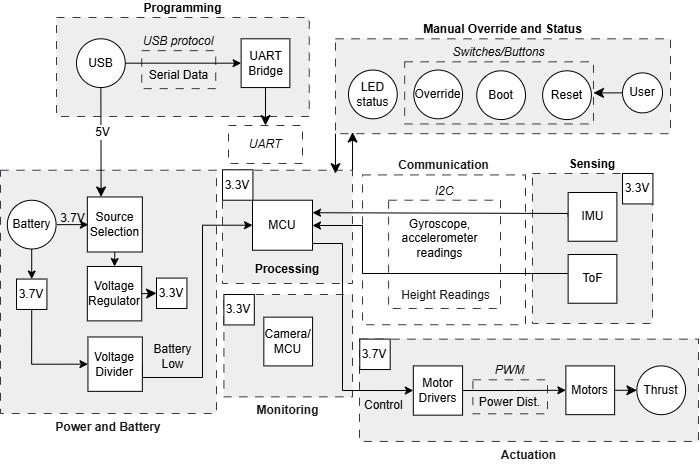
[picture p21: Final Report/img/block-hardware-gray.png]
    
    \caption{Hardware Architecture}
    \label{fig:block-hardware}
\end{figure}

A description of each of the architectural elements is given below in Table~\ref{tab:hardware-arch}.  ach element of the hardware architecture supports a specific functional or safety requirement, as outlined in Table~\ref{tab:hardware-arch}. Additionally, the \gls{pcb} design must maintain signal integrity, minimise power losses, and allow efficient component routing (R.15). The structural frame supports the \gls{pcb}, battery, and motors, incorporating propeller guards to satisfy safety requirements (R.17).

\begin{table}[H]
\centering
\caption{Hardware Elements and Requirements}
\label{tab:hardware-arch}
\begin{tabular}{|m{0.25\textwidth}|m{0.50\textwidth}|m{0.20\textwidth}|}
\hline
\rowcolor{gray!15}
\textbf{Architectural Element} & \textbf{Purpose} & \textbf{Requirement(s)} \\
\hline
Actuation and Sensing & Provides continuous data needed for state estimation (position and orientation of the drone), control stability, and safety. & R.2, R.1, R.3, R.4, R.20, R.5, R.21 \\
\hline
Power and Battery  & Regulates power supply input and manages power from battery. & R.27, R.18 \\
\hline
Processing, Programming, Communication & \gls{mcu} executes control loops and manages peripheral communication. \newline
Programming allows firmware upload and monitoring of diagnostics. \newline
Communication provides telemetry between sensors, actuators, and processing tasks. & All except R.17, R.14, R.18, R.15 \\
\hline
Actuation & Converts control signals into thrust outputs. & R.2, R.1, R.4, R.27, R.29, R.5 \\
\hline
Manual Override and Status & Provides manual override and status via LEDs. & Additional \\
\hline
Monitoring & Provides a means for surveillance of the environment. & Additional \\
\hline
\end{tabular}
\end{table}

%-------------------------------------------------------------%
\subsubsection{Hardware Justification}

The architecture was informed by several open-source designs, including CircuitDigest’s ESPDrone \cite{espdrone_circuitdigest}, Espressif’s ESP-Drone \cite{espdrone_espressif}, and Max Imagination’s ESP-FLY \cite{maximagination}, alongside Espressif’s official ESP32 DevKit schematics \cite{espressif_devkits}. These references provided practical guidance for lightweight drone design, component selection, and standard circuit integration. The final design integrates these layouts with project-specific adaptations to meet the functional and safety requirements of this project. The design elements and the rationale behind them is given in Table~\ref{tab:hardware-justification}.

\renewcommand{\arraystretch}{1.2}
\begin{table}[H]
\centering
\caption{Design Element Justification}
\label{tab:hardware-justification}
\begin{tabular}{|p{0.18\textwidth}|p{0.82\textwidth}|}
\hline
\rowcolor{gray!15}
\textbf{Element} & \textbf{Rationale} \\
\hline
Power and Battery & The ESP32 requires a stable 3.3\,V supply. A source selection circuit allows both battery and \gls{usb} connection, with priority given to \gls{usb}. Battery low level is monitored via simple voltage divider to warn when charge is low. \\
\hline
Programming & Firmware uploading and debugging require a \gls{usb}-to-\gls{uart} bridge, providing direct serial communication with the \gls{mcu}. \\
\hline
Sensing and Communication & An \gls{imu} is necessary for flight stability and position control. A \gls{tof} sensor simplifies height measurement and reduces error accumulation from integration. Sensors use standard protocols such as I\textsuperscript{2}C for reliable communication with the \gls{mcu}. \\
\hline
Actuation & \gls{dc} motors controlled via \gls{pwm} generate thrust. Individual motor control ensures balance and stabilisation. Simple motor driver circuits (\glspl{ic} or \gls{mosfet} switches) provide reliable control for each motor. \\
\hline
Monitoring & A separate \gls{mcu} for the surveillance camera ensures independent processing from the flight controller for modularity. \\
\hline
Manual Override and Status & Physical switches and LEDs provide user feedback and safety. Manual power-off allows immediate shutdown. Status LEDs indicate power and connectivity. \\
\hline
\end{tabular}
\end{table}

%----------------------------------------------------------------%
\subsubsection{Firmware Architecture}
The firmware architecture defines the drone’s control logic and operational behaviour. It manages sensor acquisition, state estimation, and motor actuation within a real-time stabilisation loop. Sensor fusion combines \gls{imu} and time-of-flight (\gls{tof}) data to estimate orientation and altitude, while cascaded \gls{pid} controllers maintain attitude and height stability.  

A WebSocket-based communication layer enables remote telemetry and command control via a Wi-Fi access point. Safety routines include manual override and automatic motor shutdown in case of communication loss or detected fault conditions.

\begin{figure}[H]
    \centering
    \captionsetup{justification=centering, margin=1cm}
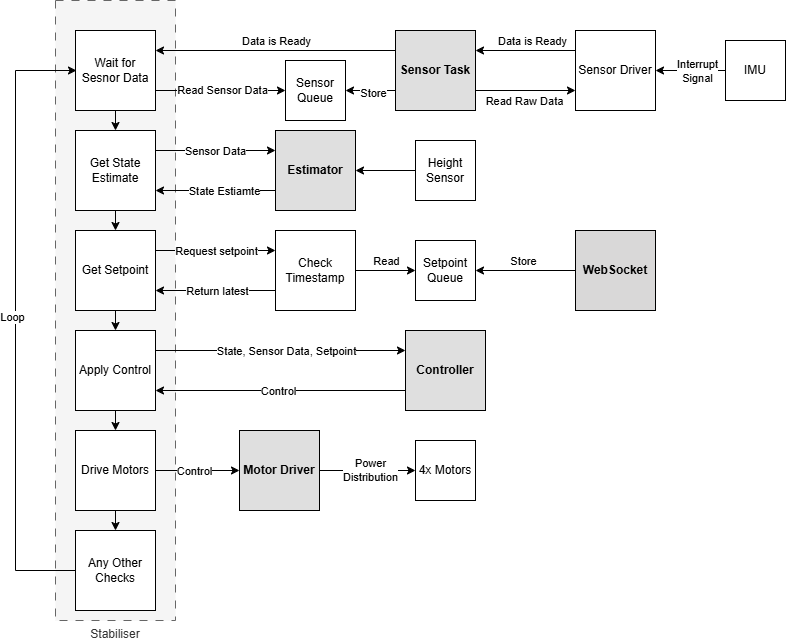
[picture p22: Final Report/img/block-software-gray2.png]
    
    \caption{Firmware Architecture}
    \label{fig:block-software}
\end{figure}

%----------------------------------------------------------------%
\subsubsection{Firmware Justification}

Firmware using the ESP32 was reviewed for the firmware architecture including Espressif’s ESP-Drone (or more so, Circuit Digest’s modified version~\cite{espdrone_circuitdigest}, with fixed UDP driver needed for Crazyflie Client (CFClient)). It is built on the \gls{esp-idf} framework and derived from the Crazyflie open-source project (GPL-3.0)~\cite{bitcraze_crazyflie_firmware} and was assessed as a baseline for stable flight and mobile control. Phadte’s ESP32 Flight Controller~\cite{pratikphadte_flight_controller} developed with the Arduino framework, was reviewed as a simple custom implementation of a flight controller, built for a larger brushless motor drone, and the \gls{pid} tuning methodology.  

Based on this analysis, a custom firmware was developed using \gls{esp-idf} v5.5.0 to provide long-term flexibility, low-level control, and improved integration. This approach simplified the generalised Crazyflie libraries of ESP-Drone, which contain dozens of source files and many macros and generalisations to work with multiple drone designs. Then, the lower-level \gls{esp-idf} environment was chosen over Arduino to achieve more precise timing, and compatibility with \gls{esp-idf} libraries.

This configuration ensures stable flight under constrained indoor conditions while maintaining extensibility for future autonomous functionality and research development within the \gls{uwaal}.

\begin{table}[H]
\centering
\renewcommand{\arraystretch}{1.2}
\caption{Firmware Option Comparison}
\begin{tabular}{|>{\bfseries}p{0.17\textwidth}|p{0.2\textwidth}|p{0.2\textwidth}|p{0.2\textwidth}|}
\hline
\rowcolor{gray!15}
\textbf{Feature} & \textbf{ESP-Drone} & \textbf{Phadte} & \textbf{Custom} \\
\hline
Framework & \gls{esp-idf} v4.4.8 & Arduino & \gls{esp-idf} v5.5.0 \\
\hline
Control Type & Manual & Manual & Manual/Autonomous \\
\hline
Complexity & High & Low & Moderate \\
\hline
Flexibility & Moderate & Low & High \\
\hline
Integration & \gls{esp-idf} libraries & Arduino libraries & \gls{esp-idf} libraries \\
\hline
Primary Focus & General purpose & Flight stabilisation only & Project specific \\
\hline
\end{tabular}
\end{table}

The final architecture balances flexibility and control, centring on a stabilisation loop that integrates \gls{imu} feedback, cascaded \gls{pid} control, and motor actuation derived from the Crazyflie core library, as shown in Fig.~\ref{fig:block-software}.

\begin{table}[H]
\centering
\caption{Firmware Architecture Rationale}
\renewcommand{\arraystretch}{1.2}
\begin{tabular}{|p{0.16\textwidth}|p{0.25\textwidth}|p{0.49\textwidth}|}
\hline
\rowcolor{gray!15}
\textbf{Element} & \textbf{Purpose} & \textbf{Rationale} \\
\hline
Sensor Task & Acquire data from onboard sensors. & Sensor inputs are required to estimate the drone’s state. \gls{imu} and \gls{tof} sensors were used to meet project requirements while remaining compatible with open-source third-party software if needed. \\
\hline
State Estimator & Combine sensor inputs to estimate attitude (roll, pitch, yaw) and altitude. & State estimation is necessary for the drone to determine its orientation, needed for stabilisation. \\
\hline
Motor Driver & Convert control signals into motor speed commands via \gls{pwm} or driver interface. & Motor control generates thrust based on output from the \gls{pid} control system. \\
\hline
Override & Handle manual override, loss of communication, and fault detection. & Safety functions include fault detection, manual override, and controlled handling of errors to prevent unsafe operation. \\
\hline
Communication & Provide telemetry, control input, and data logging through WebSocket or serial link. & Communication with the WebSocket is required for remote activation or deactivation, command transmission, and system feedback. It also supports debugging and monitoring. \\
\hline
Timing/Stabiliser & Coordinate execution timing using an \gls{rtos}. & Timing management is critical for stabilisation, ensuring rapid response to changes in drone position or environment. \\
\hline
User Interface & Present data and system status to the operator via wireless connection. & The user interface enables remote deactivation, monitoring of system status, and basic control of the drone. \\
\hline
\end{tabular}
\end{table}

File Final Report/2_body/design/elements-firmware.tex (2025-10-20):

\subsubsection{Firmware Elements}

The firmware elements, shown in Fig.~\ref{fig:block-software}, are detailedbelow. The detailed implementation of these elements is given in \cite{flightcontroller_git}. To view the code as up to date with the submission of this report, refer to Appendix~\ref{app:firmware-code}.

\begin{figure}[H]
    \centering
    \captionsetup{justification=centering, margin=1cm}
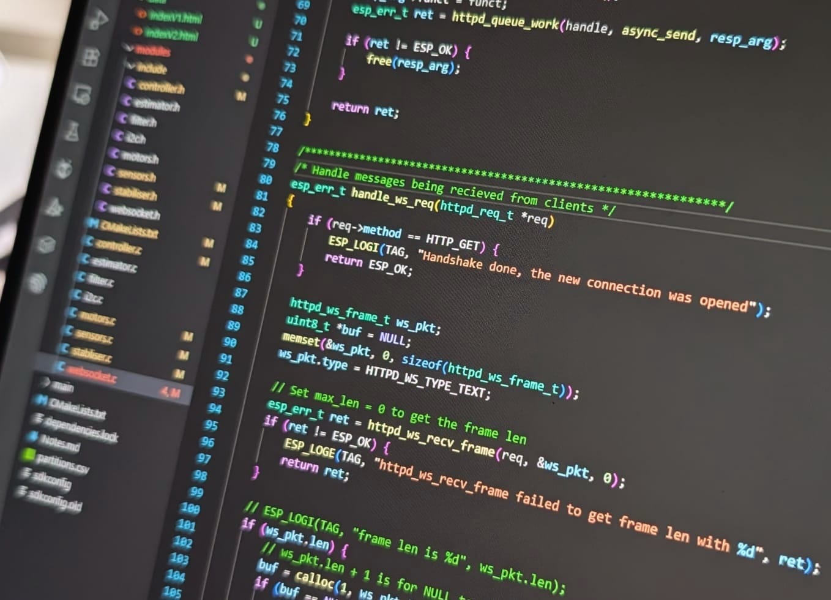
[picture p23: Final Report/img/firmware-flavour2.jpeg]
    
    \caption{\gls{esp-idf} Environment}
    \label{fig:frame}
\end{figure}

\paragraph{\textbf{Sensor Task} \textit{sensors.c}} \leavevmode

The sensor task provides an interface for the \gls{mpu6050} 6-axis \gls{imu} through \gls{i2c}, which provides real-time data from the accelerometer and gyroscope on the sensor. This is done on a register level using Espressif's \textit{I2C} library.

An \gls{isr} is attached to the \gls{mpu6050} interrupt; this means that instead of the sensor task continuously reading from the \gls{mpu6050}, it waits for the trigger to signify that data is ready to be read. The data is then stored in a queue, and an additional signal is sent to the stabiliser task to signify the processed sensor data is ready.

\begin{figure}[H]
    \centering
    \captionsetup{justification=centering, margin=1cm}
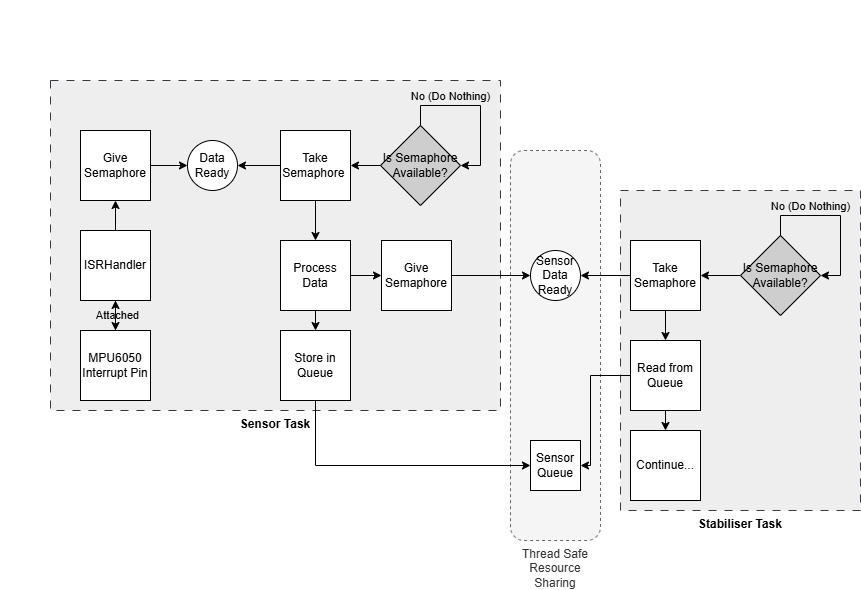
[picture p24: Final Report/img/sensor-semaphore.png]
    
    \caption{Thread-safe Data Availability Signalling Heuristic}
    \label{fig:isr}
\end{figure}

The raw data obtained from the \gls{mpu6050} sensor are 16-bit integer values representing the gyroscope and accelerometer measurements. These values are first converted into physical units (SI units) based on the selected sensitivity configuration of the sensor. The conversion from raw readings to angular velocity and linear acceleration is expressed as:

\begin{align}
\boldsymbol{\omega} &= (\mathbf{G}_{\text{raw}} - \mathbf{G}_{\text{bias}}) \times S_{\text{gyro}}, \\[6pt]
\mathbf{a} &= \mathbf{A}_{\text{raw}} \times S_{\text{acc}},
\end{align}

where \( \mathbf{G}_{\text{raw}} \) and \( \mathbf{A}_{\text{raw}} \) are the raw gyroscope and accelerometer readings, \( \mathbf{G}_{\text{bias}} \) is the gyroscope bias, which is calculated when the filter is initialised. \( S_{\text{gyro}} \) and \( S_{\text{acc}} \) are the corresponding sensitivity scaling factors.

To reduce measurement noise, a second-order digital biquad low-pass filter is applied to the sensor data. This filter attenuates high-frequency noise while preserving the motion dynamics of interest. Cutoff frequencies of 30\,Hz and 80\,Hz are used for the accelerometer and gyroscope, respectively. Additionally, the \gls{mpu6050} incorporates an internal digital low-pass filter on the gyroscope measurements, which is also enabled for further signal smoothing. The digital biquad filter can be expressed in the $z$-domain as:

\begin{align}
H(z) &= \frac{b_0 + b_1 z^{-1} + b_2 z^{-2}}{1 + a_1 z^{-1} + a_2 z^{-2}}, \\[6pt]
w(n) &= x(n) - a_1 w(n-1) - a_2 w(n-2), \\[6pt]
y(n) &= b_0 w(n) + b_1 w(n-1) + b_2 w(n-2),
\end{align}

where \( x(n) \) is the current input sample, \( y(n) \) is the filtered output, and \( w(n) \) represents the internal state variables in Direct Form~II. The coefficients can be found in~\ref{app:code-filter}.

\paragraph{\textbf{State Estimation} \textit{estimator.c}} \leavevmode
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

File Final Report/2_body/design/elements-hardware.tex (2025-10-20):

\subsubsection{\gls{pcb} Hardware Elements}

The hardware subsystem forms the foundation of the drone, integrating all power, control, and sensing elements on a custom \gls{pcb}. It is designed to be compact, lightweight, and serviceable while maintaining electrical reliability, \gls{emi} resilience, and thermal performance. Fig.~\ref{fig:pcb-sections} and Fig.~\ref{fig:pcb-final} illustrate the
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

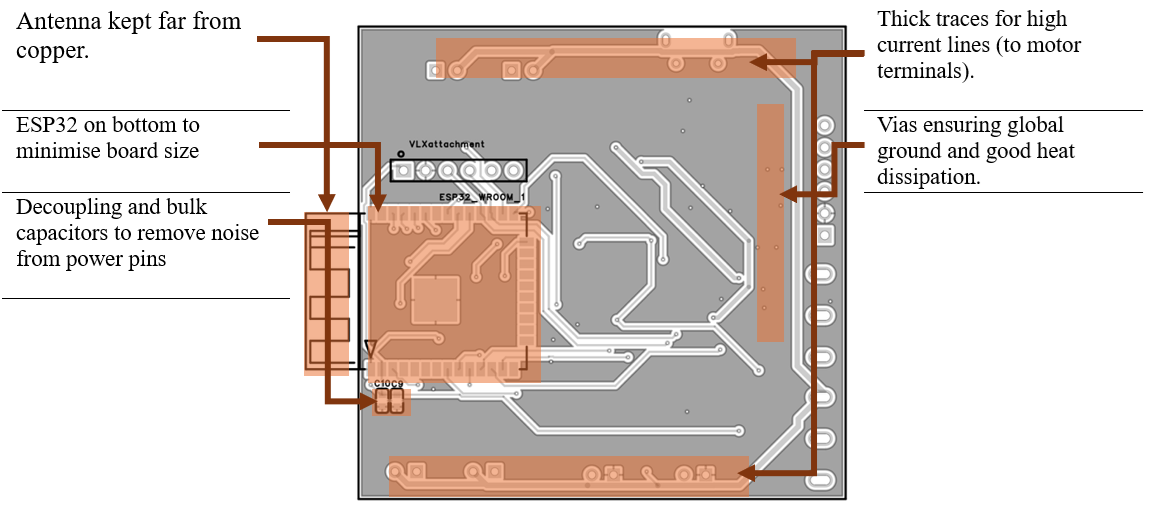
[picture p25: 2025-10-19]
Final Report/img/pcb-elements2.png

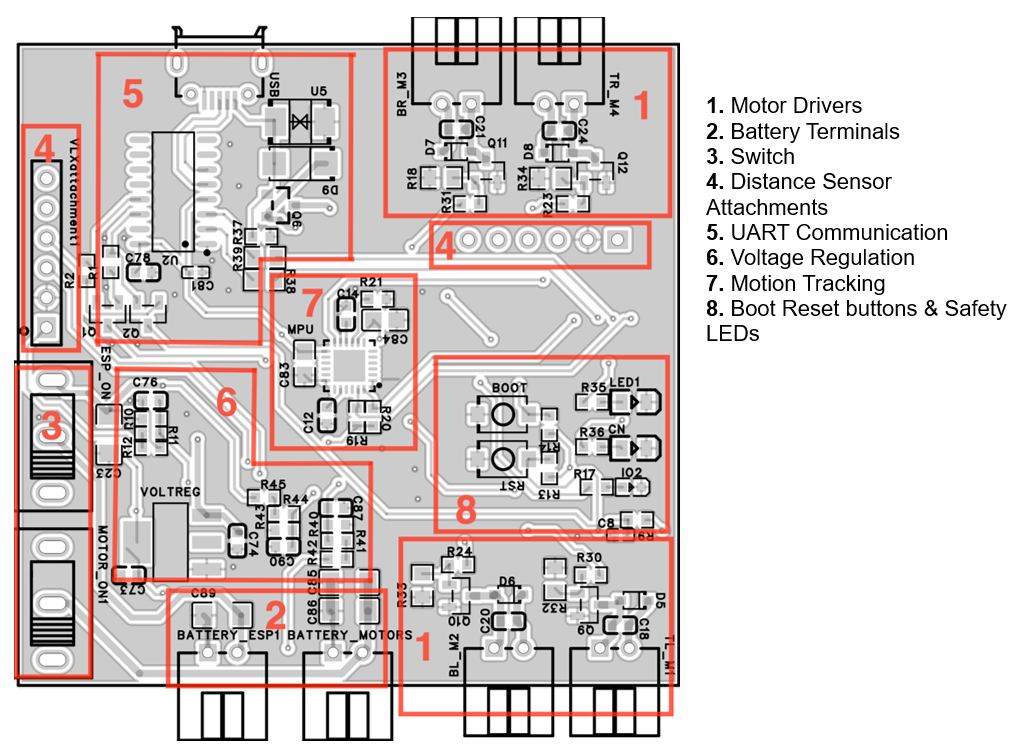
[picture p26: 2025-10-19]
Final Report/img/pcb-sections.png

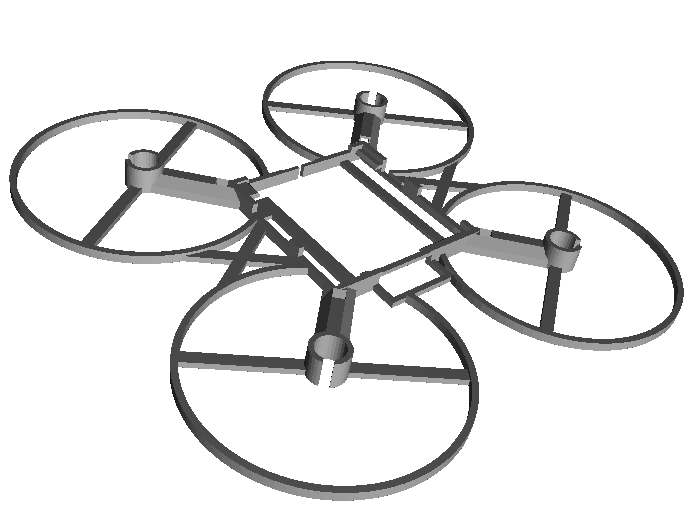
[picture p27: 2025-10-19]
Final Report/img/main-frame.png

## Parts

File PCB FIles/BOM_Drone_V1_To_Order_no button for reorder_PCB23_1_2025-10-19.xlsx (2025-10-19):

No. | Quantity | Comment | Designator | Footprint | Value | Manufacturer Part | Manufacturer | Supplier Part | Supplier | Layer | LCSC Price | JLCPCB Price
1 | 6 | 2.54mm-2P WZ | BATTERY_ESP1,BATTERY_MOTORS,BL_M2,BR_M3,TL_M1,TR_M4 | CONN-TH_2P-P2.50_HX-2.54MM-2P-WZ-1 |  | 2.54mm-2P WZ | SHOU HAN(首韩) | C5368788 | LCSC | T |  | 0.0014
2 | 2 | TS-1088-AR02016 | BOOT,RST | SW-SMD_L3.9-W3.0-P4.45 |  | TS-1088-AR02016 | XUNPU(讯普) | C720477 | LCSC | T |  | 0.0061
3 | 1 | 1uF | C8 | C0402 | 1uF | CL05A105KA5NQNC | SAMSUNG(三星) | C52923 | LCSC | T |  | 0.0005
4 | 1 | 10uF | C9 | C0603 | 10uF | CL10A106KP8NNNC | SAMSUNG(三星) | C19702 | LCSC | B |  | 0.0008
5 | 1 | 100nF | C10 | C0603 | 100nF | CC0603KRX7R9BB104 | YAGEO(国巨) | C14663 | LCSC | B |  | 0.0004
6 | 10 | 100nF | C12,C14,C18,C20,C21,C24,C76,C78,C87,C90 | C0603 | 100nF | CC0603KRX7R9BB104 | YAGEO(国巨) | C14663 | LCSC | T |  | 0.0004
7 | 4 | 47uF | C23,C85,C86,C89 | C1206 | 47uF | CL31A476MPHNNNE | SAMSUNG(三星) | C96123 | LCSC | T |  | 0.0099
8 | 2 | 22uF | C73,C74 | C0603 | 22uF | CL10A226MQ8NRNC | SAMSUNG(三星) | C59461 | LCSC | T |  | 0.0013
9 | 1 | 10nF | C81 | C0402 | 10nF | CL05B103KB5NNNC | SAMSUNG(三星) | C15195 | LCSC | T |  | 0.0002
10 | 2 | 10uF | C83,C84 | C0805 | 10uF | GRM21BR61H106KE43L | muRata(村田) | C440198 | LCSC | T |  | 0.0089
11 | 1 | KT-0805G | CN | LED0805-R-RD |  | KT-0805G | KENTO | C2297 | LCSC | T |  | 0.0016
12 | 4 | 1N4148WS | D5,D6,D7,D8 | SOD-323_L1.8-W1.3-LS2.5-RD |  | 1N4148WS | CJ(江苏长电/长晶) | C2128 | LCSC | T |  | 0.0013
13 | 1 | SS34 | D9 | SMA_L4.3-W2.6-LS5.2-RD |  | SS34 | MDD(辰达半导体) | C8678 | LCSC | T |  | 0.004
14 | 1 | ESP32-WROOM-32 | ESP32_WROOM_1 | WIFIM-SMD_ESP-32S |  | ESP32-WROOM-32 | ESPRESSIF(乐鑫) | C82899 | LCSC | B |  | 0.5998
15 | 2 | SS12D10G5 | ESP_ON,MOTOR_ON1 | SW-TH_SHOU-HAN_SS12D10G4 |  | SS12D10G5 | SHOU HAN(首韩) | C7431054 | LCSC | T |  | 0.0224
16 | 1 | KT-0603R | IO2 | LED0603-RD |  | KT-0603R | KENTO | C2286 | LCSC | T |  | 0.0008
17 | 1 | KT-0805W | LED1 | LED0805-R-RD |  | KT-0805W | KENTO | C34499 | LCSC | T |  | 0.0026
18 | 1 | MPU-6050 | MPU | QFN-24_L4.0-W4.0-P0.50-BL-EP2.7 |  | MPU-6050 | TDK InvenSense(应美盛) | C24112 | LCSC | T |  | 0.9579
19 | 2 | SS8050(RANGE:200-350) | Q1,Q2 | SOT-23-3_L2.9-W1.3-P1.90-LS2.4-BR |  | SS8050(RANGE:200-350) | CJ(江苏长电/长晶) | C2150 | LCSC | T |  | 0.0019
20 | 1 | AO3401A | Q6 | SOT-23_L2.9-W1.3-P1.90-LS2.4-BR |  | AO3401A | AOS | C15127 | LCSC | T |  | 0.008
21 | 4 | AO3400A | Q9,Q10,Q11,Q12 | SOT-23-3_L2.9-W1.3-P1.90-LS2.4-BR |  | AO3400A | AOS | C20917 | LCSC | T |  | 0.0102
22 | 7 | 10kΩ | R1,R2,R9,R13,R14,R19,R20 | R0603 | 10kΩ | 0603WAF1002T5E | UNI-ROYAL(厚声) | C25804 | LCSC | T |  | 0.0002
23 | 10 | 100kΩ | R10,R11,R12,R37,R40,R41,R42,R43,R44,R45 | R0603 | 100kΩ | 0603WAF1003T5E | UNI-ROYAL(厚声) | C25803 | LCSC | T |  | 0.0002
24 | 3 | 1kΩ | R17,R35,R36 | R0603 | 1kΩ | 0603WAF1001T5E | UNI-ROYAL(厚声) | C21190 | LCSC | T |  | 0.0002
25 | 4 | 100kΩ | R18,R32,R33,R34 | R0805 | 100kΩ | WR08X1003FTL | Walsin(华新科) | C132377 | LCSC | T |  | 0.0003
26 | 1 | 5.6kΩ | R21 | R0603 | 5.6kΩ | 0603WAF5601T5E | UNI-ROYAL(厚声) | C23189 | LCSC | T |  | 0.0002
27 | 4 | 10Ω | R23,R24,R30,R31 | R0603 | 10Ω | WR06X10R0FTL | 华新科(Walsin) | C163851 | LCSC | T |  | 0.0002
28 | 2 | 10Ω | R38,R39 | R0805_NEW | 10Ω | 0805W8F100JT5E | UNI-ROYAL(厚声) | C17415 | LCSC | T |  | 0.0003
29 | 1 | CH340C | U2 | SOP-16_L10.0-W3.9-P1.27-LS6.0-BL |  | CH340C | WCH(南京沁恒) | C84681 | LCSC | T |  | 0.0744
30 | 1 | SMBJ6.5CA | U5 | SMB_L4.6-W3.5-LS5.3-BI |  | SMBJ6.5CA | 宏嘉诚 | C7420377 | LCSC | T |  | 0.0059
31 | 1 | USB-MICRO XNJ JB | USB | MICRO-USB-SMD_HX-USB-MICRO-XNJ-JB |  | USB-MICRO XNJ JB | SHOU HAN(首韩) | C7507410 | LCSC | T |  | 0.0051
32 | 1 | PM2.54-1*6 | VLXattachment | HDR-TH_6P-P2.54-V-F_4 |  | PM2.54-1*6 | ZHOURI(洲日) | C5224026 | LCSC | B |  | 0.0111
33 | 1 | PM2.54-1*6 | VLXattachment1 | HDR-TH_6P-P2.54-V-F_4 |  | PM2.54-1*6 | ZHOURI(洲日) | C5224026 | LCSC | T |  | 0.0111
34 | 1 | AMS1117-3.3 | VOLTREG | SOT-223-3_L6.5-W3.4-P2.30-LS7.0-BR |  | AMS1117-3.3 | AMS | C6186 | LCSC | T |  | 0.0235

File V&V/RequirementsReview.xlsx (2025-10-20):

ID | Requirement description | Test | Passed | Learnings
Example | Completed system module will withstand vibrations up to 3g | Mount module of shock generator module capable of producing 3g | YES | The requirement initially specified only a g-value. However, the client expected the to test a frequency range up to 300Hz, and this did not come across completely during communications. Whilst the test was set up correctly for the requirement as-defined, and does allow the requirement to be tested, the shock-generator can only produce single-shocks and does not allow measurement of the frequency-dependent rejection of external vibrations. Therefore the test did not satisfy the clients original expectations.
Primary
R.2. | The drone shall be capable of hovering and flying | Apply power to motors, with both manual control and stabilised control with the drone able to liftoff and turn. | No | N/A
R.30 | The drone must power off after 30s of disconnection | Manually disconnect the drone and check if the Drone has powered off after 30s | Yes | The requirements specify that a manual disconnection should occur after 30 seconds. However, in manual command mode, this threshold should be reduced to a much shorter duration, typically less than one second. Complete verification of this behaviour was not possible, as the disconnection tests were conducted without the drone in flight. Consequently, the tests did not account for realistic operational conditions or associated safety considerations.
R.1. | The drone shall operate in an indoor area. | N/A | Yes | The drone is designed for indoor use with small motors, propellers, battery and propeller gaurds.
R.17. | The drone shall utilise shrouded propellers or dedicated propeller guards | Drop drone onto propeller shouds from 2m onto hard concrete to check for durability and ability to guard propellers against collisions | Yes | 2 m drops concentrate load at ring-arm roots, the first failures were that the shrouds printed too thin, resulting in snapping or bending. Increasing the wall to 2.0mm and printing ring supports improved survivability. Now survives impact with no bending, ensuring propeller clearance.
R.3. | The drone shall navigate without the use a Global Positioning System (GPS). | The drone must be able to show its orientation and altitude on a websocket using on onboard MPU. Display must be within 5% of true position (angle) after 3 minutes of hovering. | No | Gyro bias drift dominated the first 2 min occurrences, but it was not significant until after 2 minutes. WebSocket latency doesn’t affect the estimate, but confuses the display during sudden changes. True testing while the drone is hovering has not been conducted.
R.4. | The drone shall maintain a set hovering altitude during autonomous surveillance. | After a setpoint the drone should not deviate from that position by 20cm or 30cm with wind over the span of 30s | No | Without the stable liftoff this could not be tested.
R.14. | A manual override system shall be available to the user | After automatic hovering is engaged the drone must show that the manual override can be engaged consistantly over 30 test runs. | Yes | Override engaged successfully after every test run.
R.27. | The drone shall be able to autonomously land safely where battery levels are low. | See R.2. | No | N/A
R.24. | Any third-party software used for the drone control system must be open-source and freely available. | N/A | Yes | All software can be made available on a public github.
R.23. | The drone design shall remain in a budget of $350.00 | N/A | Yes | All purchases are tracked and the total costs should remain below $350
R.20. | The drone shall be capable of flight stabilisation | See R.2. | No | N/A
R.5. | The drone shall maintain a default altitude of between 1.2 and 1.3 metres above ground level while surveying an area | See R.2. | No | N/A
R.18. | The power supplied shall be via one 1S or 2S Li-Po battery with capacity up to 800mAh. | The drone must be able to run all functions and be powered by a 1/2S battery of 800mAh, and keep motors running for 3 minutes. | Yes | Margin is tight at 1S under peak load, have a brown-out logging; confirm connector/keying and reverse-polarity protection. Drone should be capable of flight under 1S battery
R.15. | The drone shall have a custom PCB design for the flight controller which includes sensors and power distribution. | The PCB is tested for consistent 3.3V on power rails, and signal integrity is to be maintained such that the ESP32 can read the sensor value accurately | Yes | Keep local decoupling near ESP32 and MPU. Maintain clean ground returns away from motor drivers, and isolate signal lines from noisy lines. Note I²C pull-ups and routing to prevent EMI-induced read errors.
R.21. | The drone shall be able to maintain stability under wind conditions and disturbances. | See R.2. | No | N/A
Additional
R.16. | The PCB shall include custom motor drivers | The motors should reflect the PWM outputted by the ESP32. The drivers should not produce enough noise to disturb signal lines | Yes | After setting software setting the PWM to different speeds, the motor reflects these changes. Adding 10 Ω gate resistors and close flyback diodes cut dV/dt ringing and small RC snubber across the motor removed residual spikes. Copper pours hold local temperatures < 80 °C. Ensured ESP32 EN/IO0 were decoupled from PWM edges to avoid boot glitches.
R.19. | The drone shall be able to fly for a minimum of 3 minutes. | See R.2. | No | N/A
R.28. | The surveillance camera shall stream the live camera feed. | Has not been tested/implemented | No | This feature can be implemented, but the hovering and flight stabilisation requirements were prioritised.
R.26. | The UI shall have a battery level monitoring system available for low battery levels. | Has not been tested/implemented | No | N/A
R.29. | The surveillance camera shall record video for playback | See R.28 | No | N/A
R.25. | The UI shall have an error diagnostic and feedback system. | After errors are manually triggered, the UI system should show the errors as well as other applicable system information. | Yes | Errors were reliably detected after inducing faults with timestamps and priorities (critical > warning. The errors are exported to serial/WebSocket helped debug. Clear human-readable labels mapped from codes. Allows for live user reactions to errors.
R.6. | The hovering altitude shall be adjustable prior to the drone beginning operation (between 0.5 and 2 metres) | See R.2. | No | N/A
A.R.2. | The required drone operational capabilities shall be powered with only one battery. | The drone must be able to run all functions and be powered by a single battery, and keep motors running for 3 minutes. | Yes | See R.18
A.R.4. | A comprehensive operation manual and user guide shall be provided to the client for understanding, usage and further development. | A manual and comprehensive use guide should be easily accessible and avaliable on GitHub and Teams | Yes | Github available to sync firmware and documentation, includes quick-start and common issues notes.
A.R.6. | Placement of the components on PCB shall minimise signal distortion and heating for accurate flight paths and predictable behaviour. | With all components operating on the PCB, signals should still be readable to the ESP32 with accuracy of 5% | Yes | Keep local decoupling near ESP32 and MPU. Maintain clean ground returns away from motor drivers, and isolate signal lines from noisy lines. Note I²C pull-ups and routing to prevent EMI-induced read errors.
A.R.7. | The drone shall have a visual indication (LED) or audible system that warns personnel during initiation of flight. | LEDs on board the drone should be visible from 0.5m away in a well lit room | Yes | LEDs are clearly visible in normal indoor lighting from 0.5m away. LEDs can be ajusted in brightness by increasing the PWM of the LED power signal.
A.R.8. | The drone shall alert on the UI in cases over overheating. | Has not been tested/implemented | No | N/A
A.R.9. | The drone shall have LEDs to show when it is in charging mode. | Has not been tested/implemented | No | N/A
A.R.10. | The drone shall have visual or UI indicators to show when it is powering down or when it is operating autonomously. | Has not been tested/implemented | No | This feature can be implemented, but the hovering and flight stabilisation requirements were prioritised.
 |  |  |  |  | ---

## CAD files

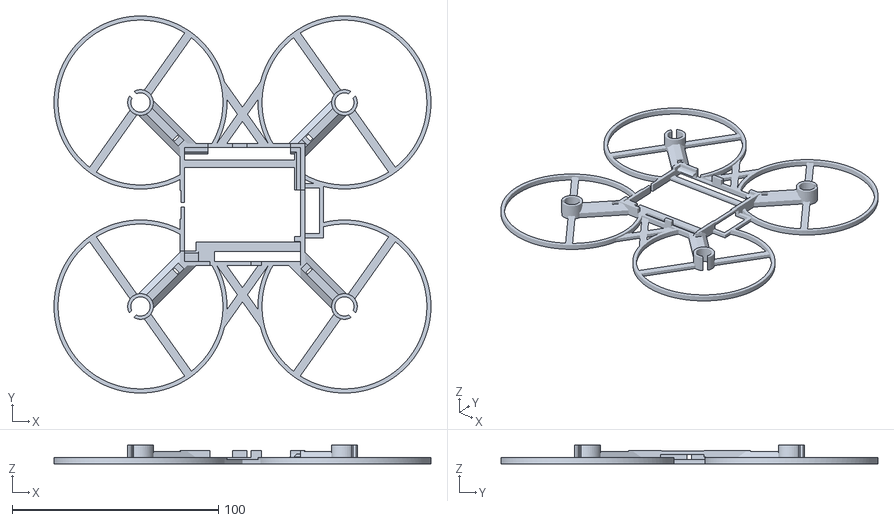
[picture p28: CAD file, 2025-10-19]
Frame/main_frame.stl
183.0 x 183.0 x 9.00

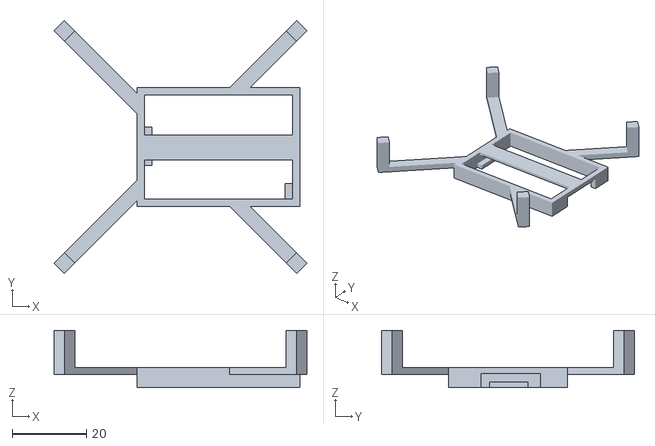
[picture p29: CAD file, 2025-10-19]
Frame/camera_mount.stl
68.3 x 68.3 x 15.5

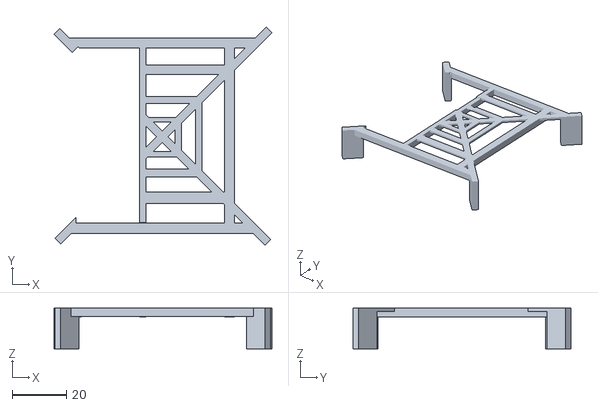
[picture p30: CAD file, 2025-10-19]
Frame/battery_cage.stl
80.2 x 80.4 x 15.0

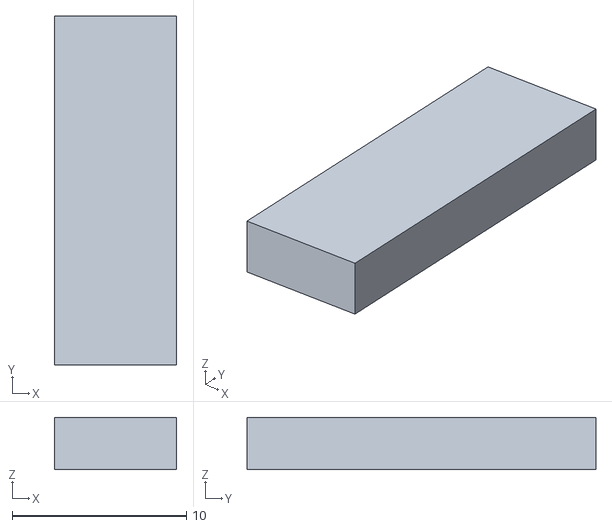
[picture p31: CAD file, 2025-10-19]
Frame/leg.stl
7.00 x 20.0 x 3.00

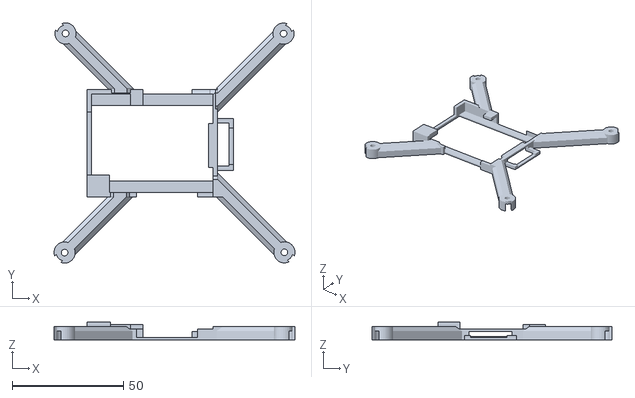
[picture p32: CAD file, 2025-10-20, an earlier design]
Prototypes/OldFrame_fitsPBC2 2.stl
108.1 x 107.8 x 8.00

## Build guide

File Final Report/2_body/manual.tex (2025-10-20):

\begin{manualblock}[Assembly Manual]

\subsection*{PCB Ordering \& Assembly Scope}
PCB should be ordered using Gerber files, Pick \& Place, and BOM. Select a 1.6\,mm PCB with standard solder mask and silkscreen colours. The top face should be assembled, with the \textbf{switch} and \textbf{female header pins} left unpopulated for hand-soldering.

\subsection*{Bill of Materials (Selected Items)}
\begin{longtable}{@{}m{2.2cm}m{1cm}m{2cm}m{1cm}m{4.5cm}m{2.5cm}@{}}
\toprule
\textbf{Item} & \textbf{Designator} & \textbf{Value/Spec} & \textbf{Qty} & \textbf{Notes / Supplier Ref.} & \textbf{Image}\\
\midrule
Female Header (PM2.54-1*6) & --- & 2.54\,mm socket & 1 & LCSC: \texttt{PM2.54-1*6} & \\
WR-PHD 2.54\,mm Socket Header & --- & 2.54\,mm & 1 & DigiKey: \texttt{613006143121} & \\
ESP32-WROOM-32 & --- & --- & 1 & LCSC: \texttt{ESP32-WROOM-32} & \\
Capacitor & C9 & 10\,\textmu F & 1 & LCSC: \texttt{CL10A106KP8NNNC} & \\
Capacitor & C10 & 100\,nF & 1 & LCSC: \texttt{CC0603KRX7R9BB104} & \\
Insulated Wire & -- & 16\,guage & 10cm & --- & \\
E-Switch & SW1/2 & 4\,A max & 1 & DigiKey: \texttt{R4ABLKREDFF0} & \\
\bottomrule
\end{longtable}

\pagebreak
\subsection*{Unboxing \& Visual Inspection Checklist}
\checkbox{} Humidity sensing paper indicates no moisture; packaging shows no mechanical damage.

\checkbox{} Inspect all soldered joints for bridges or opens; reflow or add solder as needed.

\checkbox{} Continuity: verify no shorts between \texttt{3.3V$\rightarrow$GND}, \texttt{5V$\rightarrow$GND}, \texttt{BATT$\rightarrow$GND}.

\checkbox{} Join test: mate the JST connector to the PCB-mounted female JST and confirm correct fit.

\subsection*{Tools \& Preparation}
\begin{itemize}
  \item Temp-controlled soldering iron (320--360\,$^{\circ}$C or per manufacturer), solder wire, solder wick.
  \item Flux; isopropyl alcohol and swabs; tweezers.
  \item Safety: fume extraction, eye protection, ESD wrist strap (for sensitive parts).
\end{itemize}

\subsection*{Through-Hole Technology (THT) Soldering}
Applicable parts: Female headers (\textit{VLXattachment1 / vlxattachment}), insulated wire, E-switch.
\begin{itemize}
  \item Apply flux to each pin/pad to promote wetting and keep solder confined to the intended land.
  \item Heat the joint (lead + pad), feed solder, then remove solder first and iron second; allow to cool undisturbed.
\end{itemize}

\begin{figure}[H]
  \centering
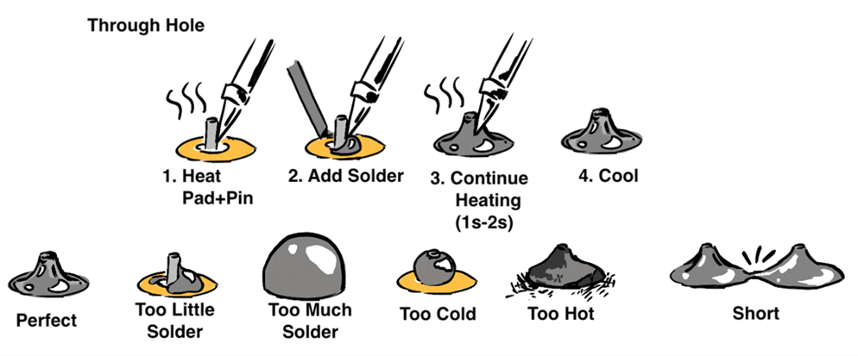
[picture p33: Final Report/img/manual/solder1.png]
  
  % \caption{Through-hole guide}
\end{figure}

\subsection*{Surface Mount Device (SMD) Soldering}
Applicable parts: Capacitors (10\,\textmu F, 100\,nF), ESP32-WROOM module.
\begin{itemize}
  \item Apply flux to pads; hold part with tweezers and tack one pad first while pressing gently to avoid tombstoning/lift.
  \item Align ESP32 module precisely; face antenna outwards (off-board edge) before reflowing all pads.
\end{itemize}

\begin{figure}[H]
  \centering
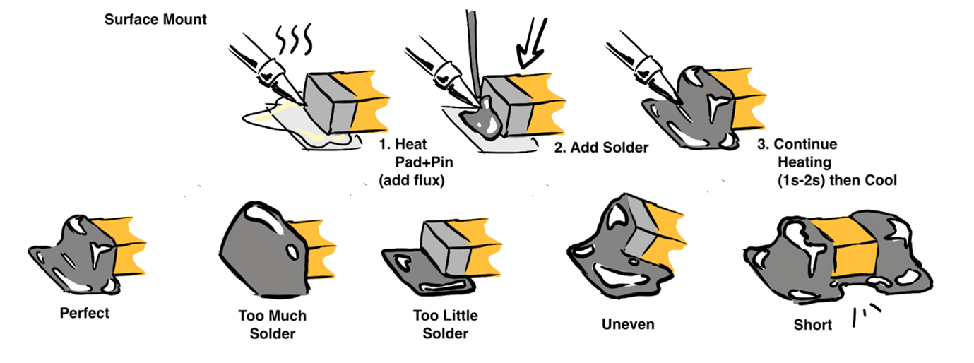
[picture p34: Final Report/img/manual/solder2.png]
  
    % \caption{SMD guide}
\end{figure}

\subsection*{Single-Battery Soldering Steps}
\subsection*{Headers \& Wiring}

\begin{figure}[H]
  \centering
  \begin{subfigure}[b]{0.48\linewidth}
    \centering
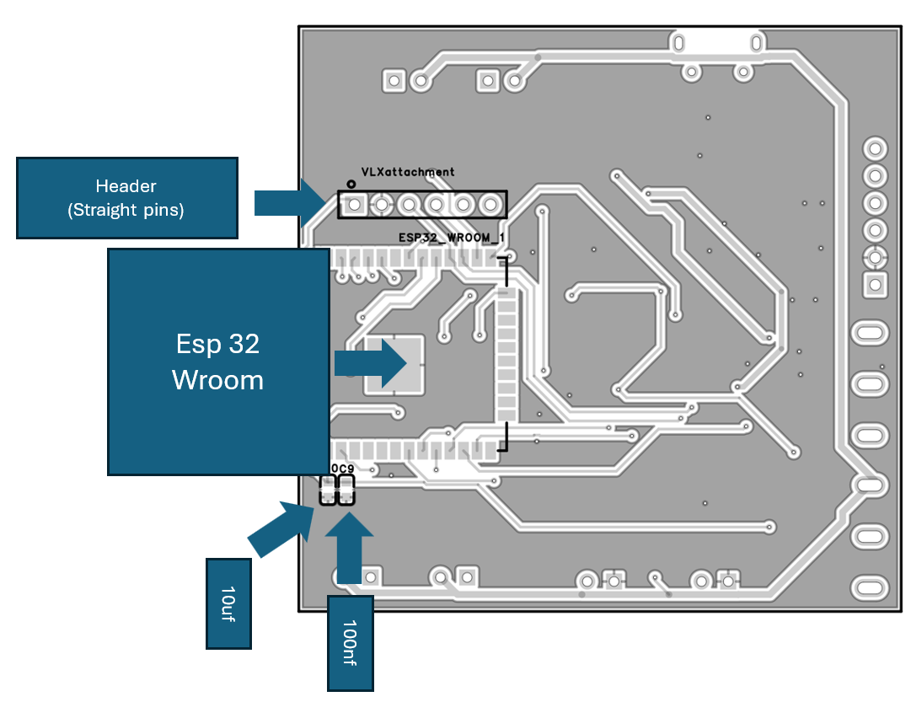
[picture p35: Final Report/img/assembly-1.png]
    
    \caption{Step 1: Front}
  \end{subfigure}
  \hfill
  \begin{subfigure}[b]{0.48\linewidth}
    \centering
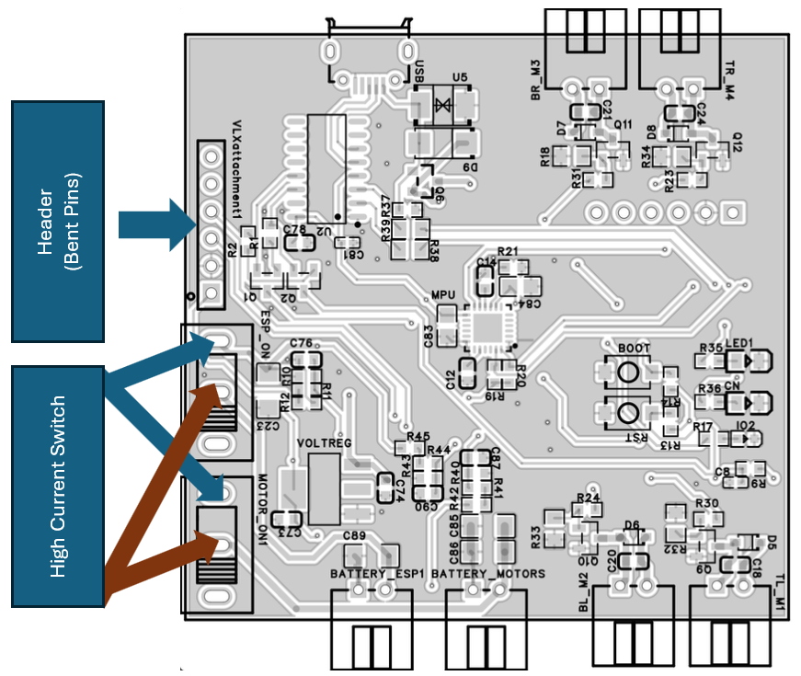
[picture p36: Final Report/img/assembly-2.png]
    
    \caption{Step 2: Back}
  \end{subfigure}
  % \caption{Component Soldering Steps}
\end{figure}

\begin{itemize}
  \item \textbf{WR-PHD 2.54\,mm Socket Header} (\textit{VLXattachment1}): THT. Feed pins through from the board side with header facing outwards; solder.
  \item \textbf{MOTOR\_ON / ESP\_ON} wiring: THT. Use insulated wire and E-switch. Ensure the \emph{ON} configuration bridges as per the diagram.
  \item \textbf{Female Header PM2.54-1*6} (\textit{vlxattachment}): THT. Feed pins through with header facing the user; solder.
\end{itemize}

\subsection*{Modules \& Passives}
\begin{itemize}
  \item \textbf{ESP32\_WROOM\_1} (ESP32-WROOM-32): SMD. Antenna faces outward past board edge; verify pad alignment prior to soldering.
  \item \textbf{C9/C10} (10\,\textmu F/100\,nF): SMD. Ensure no short across capacitor pads after soldering.
\end{itemize}

\subsection*{Rework \& Cleanup}
\begin{itemize}
  \item \textbf{Shorts}: add flux and reflow; if needed, use solder wick to remove excess and retry.
  \item \textbf{Excess/Insufficient Solder}: wick excess or add a small amount, then brief reflow.
  \item \textbf{Flux Residue}: clean with IPA-soaked swabs until pads are clean and matte.
\end{itemize}

\subsection*{Post-Soldering Verification}

\begin{figure}[H]
  \centering
  \begin{subfigure}[b]{0.48\linewidth}
    \centering
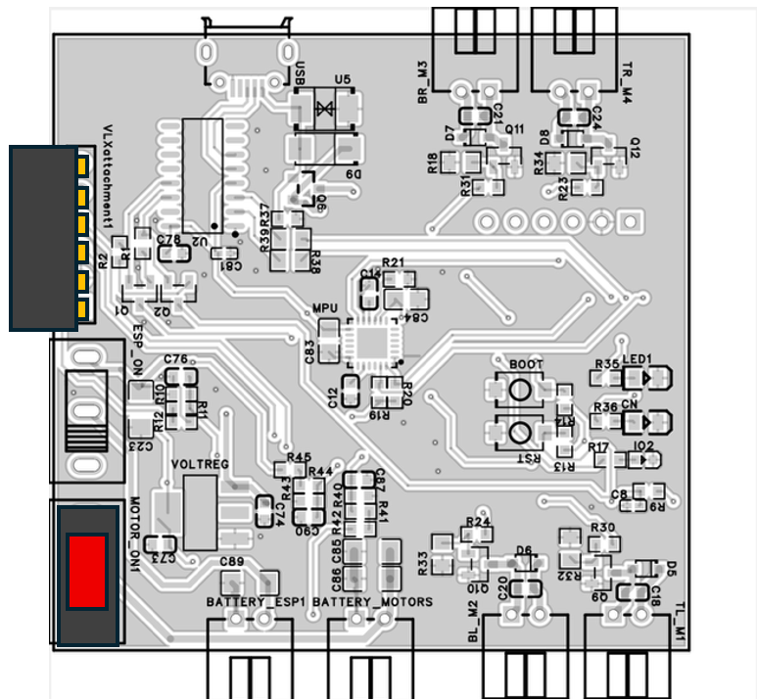
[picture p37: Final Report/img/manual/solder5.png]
    
    \caption{Step 1: Back}
  \end{subfigure}
  \hfill
  \begin{subfigure}[b]{0.48\linewidth}
    \centering
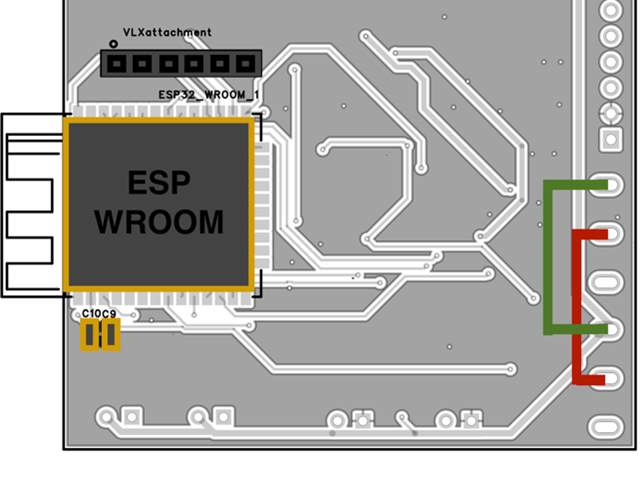
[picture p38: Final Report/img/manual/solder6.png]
    
    \caption{Step 2: Front}
  \end{subfigure}
  % \caption{Soldering Steps}
\end{figure}

\subsection*{Checklist}
\checkbox{} Continuity: all ESP32 pins are isolated (no unintended bridges).

\checkbox{} Switch continuity and actuation verified (ON/OFF as expected).

\checkbox{} C10/C9 terminal isolation confirmed (no shorts).

\checkbox{} Visual: all solder joints smooth, shiny, and confined to pad/pin.

\checkbox{} Join test: distance sensor module mates correctly in female headers.

\subsection*{3D-Printed Frame (\gls{petg})}
The frame is to be printed in \gls{petg}. Slice locally with:
\begin{itemize}
  \item Infill: 7\% (gyroid pattern).
  \item Supports: tree supports enabled.
  \item Raft: enabled for plate adhesion.
\end{itemize}

\subsection*{Print QA Checklist}
\checkbox{} Layers: consistent adhesion with no gaps.

\checkbox{} Edges: no warping present.

\checkbox{} Walls: smooth, no bumps or cracks.

\checkbox{} Bend test: parts flex slightly and return without splitting (if not, filament may be old/wet).

\begin{figure}[H]
  \centering
  \begin{subfigure}[b]{0.48\linewidth}
    \centering
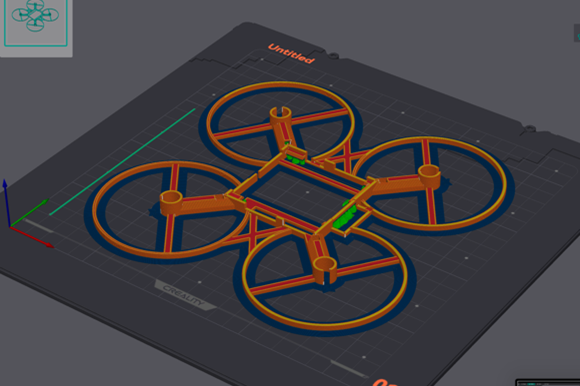
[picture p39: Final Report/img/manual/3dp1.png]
    
    \caption{Main Frame}
  \end{subfigure}
  \hfill
  \begin{subfigure}[b]{0.48\linewidth}
    \centering
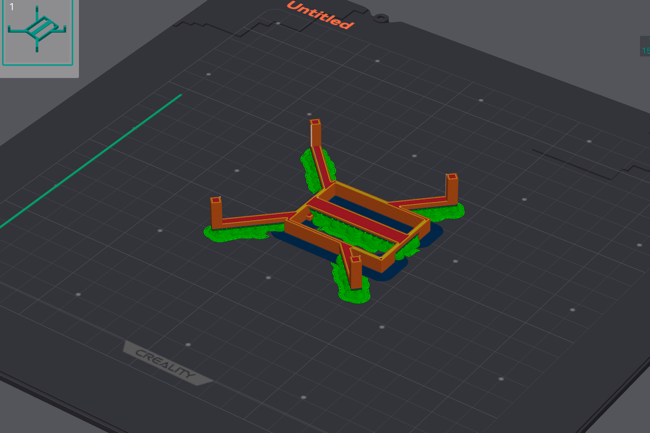
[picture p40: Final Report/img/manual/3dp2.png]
    
    \caption{Camera Mount}
  \end{subfigure}
  \begin{subfigure}[b]{0.48\linewidth}
    \centering
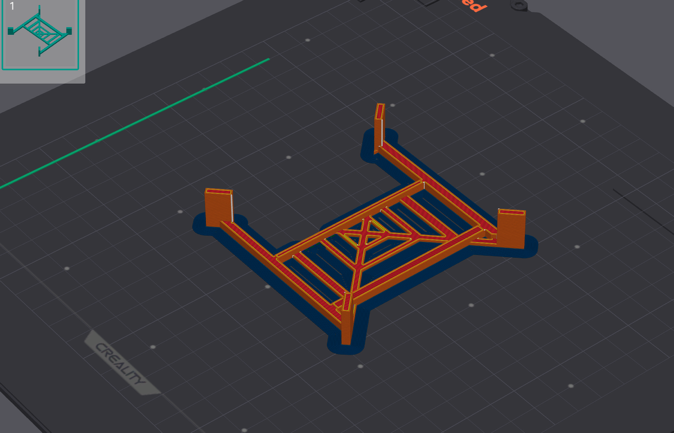
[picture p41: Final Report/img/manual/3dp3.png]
    
    \caption{Battery Cage}
  \end{subfigure}
  \hfill
  \begin{subfigure}[b]{0.48\linewidth}
    \centering
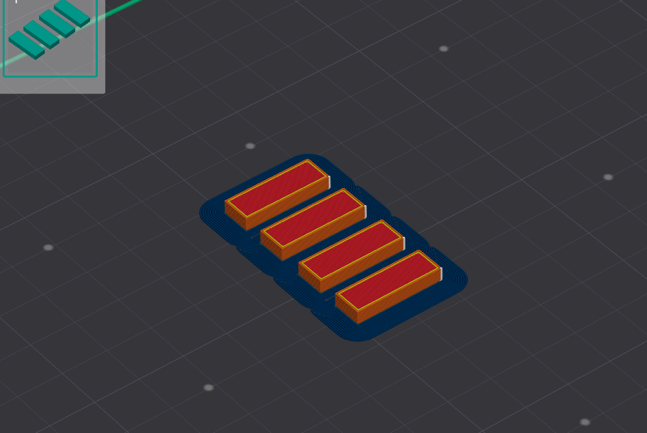
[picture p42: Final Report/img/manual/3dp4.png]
    
    \caption{Feet}
  \end{subfigure}
  % \caption{3D Printing Steps}
\end{figure}

\subsection*{Mechanical Assembly}
\begin{enumerate}
  \item \textbf{Insert PCB}: Flex the main frame slightly at the front; slide the PCB in so frame overhangs rest atop the board. Ensure overhangs do not press on or scrape components.
  \item \textbf{Attach Camera Mount}: Press onto the top of the main frame; align the front with the frame’s front.
  \item \textbf{Attach Battery Cage}: Flip the frame and press the battery cage onto the bottom; maintain correct front orientation.
  \item \textbf{Attach Legs}: Push-fit legs onto the frame.
  \item \textbf{Install Motors}: Push each motor into its hole (friction fit). Ensure CW/ACW motor pairs are mounted diagonally opposite.
  \item \textbf{Install Propellers}: Fit propellers onto matching motor directions (ACW propellers on ACW motors; CW on CW). Propellers should be tight on the shafts.
\end{enumerate}

\begin{figure}[H]
  \centering
  \begin{subfigure}[b]{0.48\linewidth}
    \centering
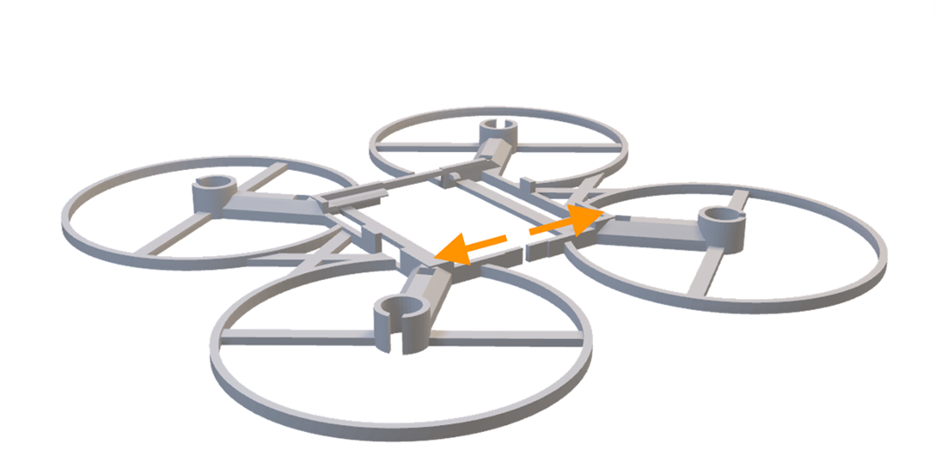
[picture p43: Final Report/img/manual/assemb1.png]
    
    \caption{Main Frame}
  \end{subfigure}
  \hfill
  \begin{subfigure}[b]{0.44\linewidth}
    \centering
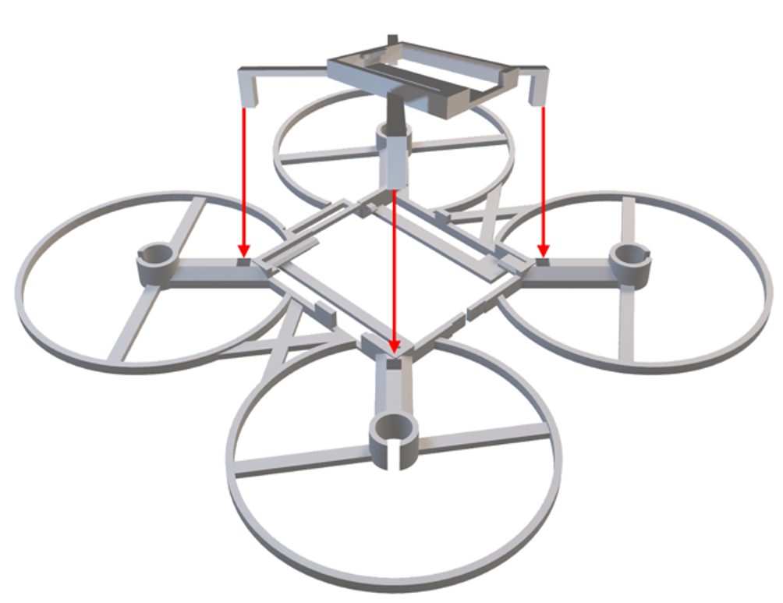
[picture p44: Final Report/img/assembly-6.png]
    
    \caption{Camera Mount}
  \end{subfigure}
  \begin{subfigure}[b]{0.44\linewidth}
    \centering
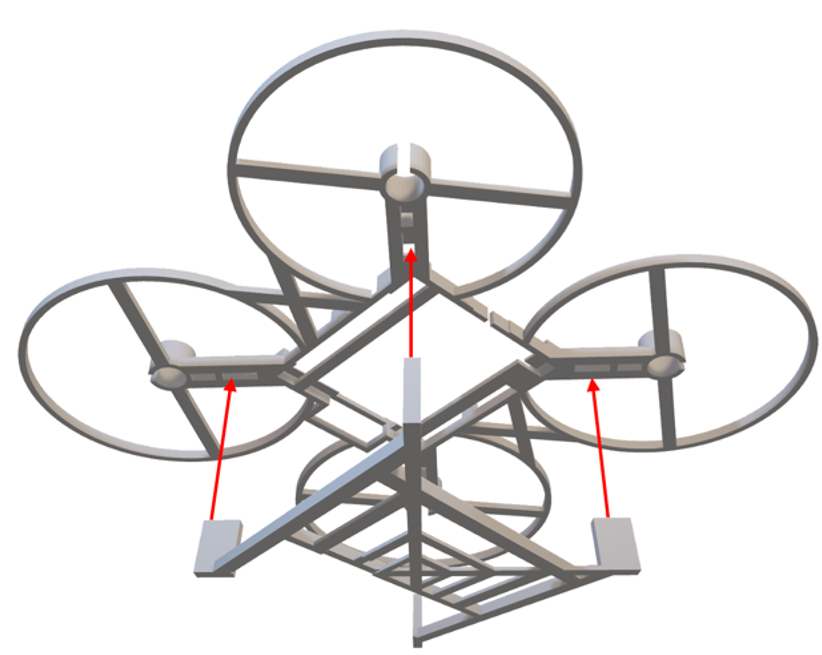
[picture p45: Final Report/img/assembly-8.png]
    
    \caption{Battery Cage}
  \end{subfigure}
  \hfill
  \begin{subfigure}[b]{0.4\linewidth}
    \centering
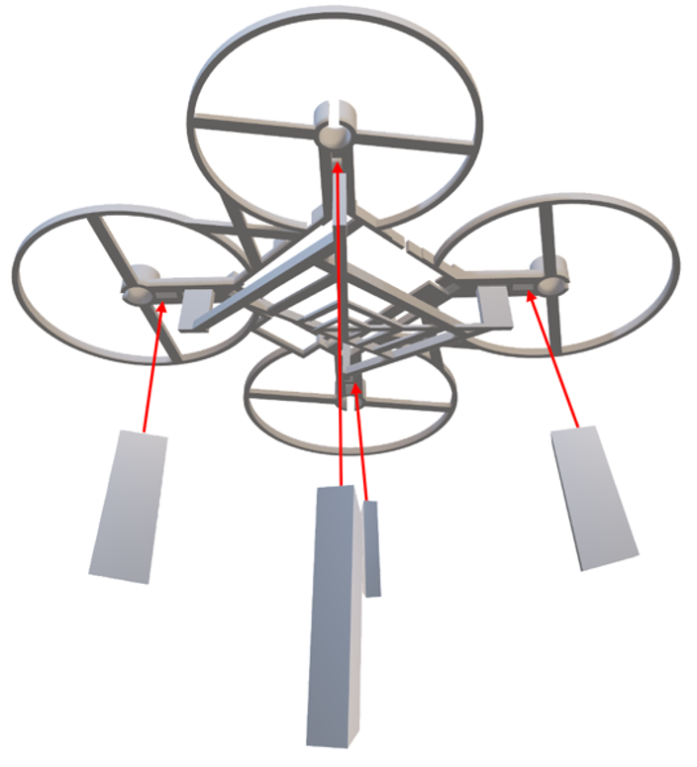
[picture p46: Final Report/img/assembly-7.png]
    
    \caption{Feet}
  \end{subfigure}
  \begin{subfigure}[b]{0.44\linewidth}
    \centering
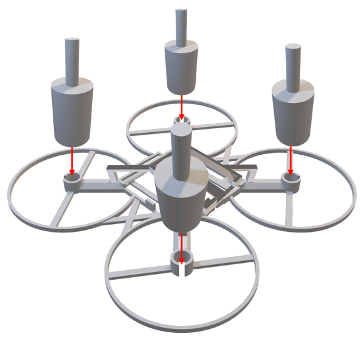
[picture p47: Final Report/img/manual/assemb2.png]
    
    \caption{Motors}
  \end{subfigure}
  \hfill
  \begin{subfigure}[b]{0.48\linewidth}
    \centering
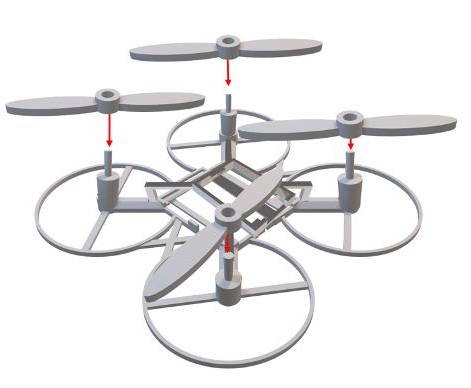
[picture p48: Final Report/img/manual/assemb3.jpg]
    
    \caption{Propellers}
  \end{subfigure}
  \caption{Assembly Steps}
\end{figure}

\subsection*{Firmware Instructions}

\subsubsection*{Uploading Firmware to Device}
\begin{enumerate}
  \item \textbf{Install ESP-IDF:} Follow the official setup guide for the ESP32-S2 series:  
  \url{https://docs.espressif.com/projects/esp-idf/en/release-v4.4/esp32s2/get-started/index.html}
  
  \item \textbf{Windows Setup:} The recommended method is using \textbf{WSL2} with the ESP-IDF extension.  
  Install WSL2 using: \url{https://learn.microsoft.com/en-us/windows/wsl/install}
  
  \item \textbf{Build Project:} Navigate to the firmware project directory in the terminal and run the build command. Ensure the firmware compiles successfully without errors.
  
  \item \textbf{Flash Firmware:} Connect the drone via micro-USB and flash the firmware using ESP-IDF tools. Wait for the device to reboot automatically after flashing.
  
  \item \textbf{Read IP Address:} Open the debug monitor to view the assigned IP address. This will be required for the WebSocket interface.
  
  \item \textbf{Configure WebSocket:}  
  Open \texttt{IndexV2.html} and update the WebSocket address to match the drone’s IP.  
  Also, update the example connection configuration with your hotspot or Wi-Fi credentials.
  
  \item \textbf{Connect:} Connect your computer to the same hotspot or Wi-Fi network. The drone should automatically connect if configured correctly.
  
  \item \textbf{Verify Connection:}  
  Open the WebSocket HTML interface in a browser. It should display that the connection is established.
  
  \item \textbf{Testing:} Press the \texttt{hello} button in the interface. If successful, the drone will return an echo message confirming communication.
\end{enumerate}

Ensure the power supply is stable during flashing. Do not disconnect the USB cable until the process is complete. Always verify Wi-Fi credentials and WebSocket settings before flight testing.

\end{manualblock}

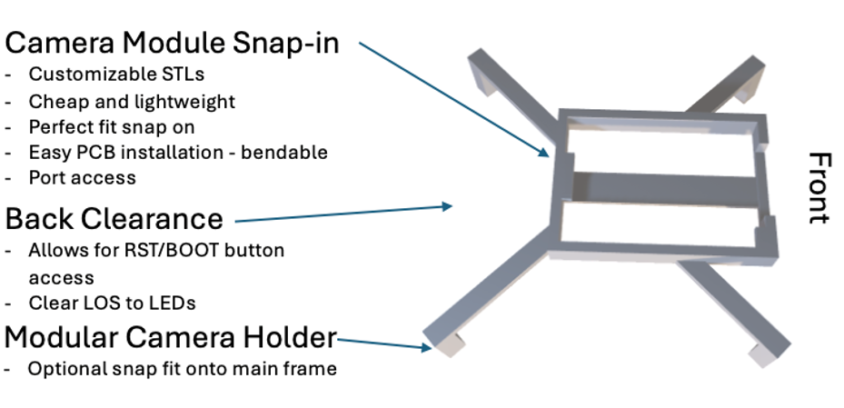
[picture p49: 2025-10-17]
Final Report/img/assembly-4.png

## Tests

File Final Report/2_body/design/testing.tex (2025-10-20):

\subsection{Testing}

Testing validated both the hardware and firmware subsystems through structured verification activities. Hardware-specific verification ensured electrical safety, EMI robustness, and mechanical reliability. Firmware-integrated tests were performed in two phases: \textit{stationary testing} to evaluate sensing, communication, and control logic, and \textit{dynamic testing} to assess flight behaviour and PID stability. 

\subsubsection{Hardware Verification and Reliability Tests}

Before final deployment, the PCB underwent detailed bench verification to ensure operational safety and design compliance. Each test corresponds to one or more design requirements (R.xx/A.R.xx) and focuses on electrical, mechanical, and thermal integrity.

\begin{longtable}{@{}p{4.2cm} p{11cm}@{}}
\toprule
\textbf{Test} & \textbf{Verification Criteria and Outcome Summary} \\ 
\midrule
\textbf{Electrical Access \& Firmware Ports} &
Flashing and monitoring possible without disassembly; no propeller interference. \newline
\textit{Pass:} $\geq$99\% flashing success over 100 cycles; no mechanical obstruction. \\ 
\midrule
\textbf{Power Regulation (5V/3.3V)} &
Voltage ripple measured under full load; brownout recovery verified. \newline
\textit{Pass:} 3.3~V within $\pm$5\%; clean reset recovery; no overheating $>85~^{\circ}$C. \\ 
\midrule
\textbf{Clock/Reset Integrity} &
POR and manual reset behaviour verified via oscilloscope. \newline
\textit{Pass:} Single monotonic reset; stable 1~h runtime without glitches. \\ 
\midrule
\textbf{Motor Driver Load Test} &
Motors driven at 100\% duty for 5~min; temperature and EMI monitored. \newline
\textit{Pass:} Case temperature $<80~^{\circ}$C; no IMU/I\textsuperscript{2}C interference. \\ 
\midrule
\textbf{I\textsuperscript{2}C Bus Integrity} &
Tested for communication stability during PWM activity. \newline
\textit{Pass:} Error rate = 0; no bus lockups. \\ 
\midrule
\textbf{\gls{rf} Keep-Out Validation} &
Antenna region visually inspected for compliance with vendor keep-out. \newline
\textit{Pass:} No metallic intrusion or ground pours detected. \\ 
\midrule
\textbf{Thermal Stability (Steady-State)} &
5~min load test in 25~°C ambient; surface temperatures measured. \newline
\textit{Pass:} ESP32~$<$60~°C, LDO/Drivers~$<$85~°C, no \gls{petg} softening. \\ 
\midrule
\textbf{Connector Retention \& Polarity} &
15~N pull test on JST and USB; polarity verification. \newline
\textit{Pass:} No lift or damage; keyed connectors prevent reverse mating. \\ 
\midrule
\textbf{Indicator LEDs (Visibility)} &
Visibility check at 0.5~m distance under indoor lighting. \newline
\textit{Pass:} All LEDs visible and distinguishable. \\ 
\midrule
\textbf{Grounding \& Layout Checks} &
Continuity probed between all ground and 3.3~V nodes. \newline
\textit{Pass:} No local ground islands; consistent rail distribution. \\ 
\midrule
\textbf{Silkscreen \& Label Verification} &
Visual inspection for component identifiers and revision markings. \newline
\textit{Pass:} All labels clear and traceable. \\ 
\bottomrule
\end{longtable}

%-------------------------------------------------------------%
\subsubsection{Firmware Verification and Reliability Tests}

\paragraph{Stationary Testing} \leavevmode

Focused on verifying hardware interfaces and firmware logic prior to flight. All components were tested under controlled, static conditions to ensure correct data acquisition and communication.

\begin{table}[H]
\centering
\renewcommand{\arraystretch}{1.2}
\begin{tabular}{|p{3.5cm}|p{12cm}|}
\hline
\textbf{Test No. \, 01} & \textbf{Sensor Functionality Test} \\ \hline
\textbf{Test Specification} & 
Verify that all onboard sensors (MPU6050 IMU and VLX distance sensor) provide accurate and consistent readings. \\ \hline
\textbf{Test Description} & 
1. Power up the drone and connect via CFClient or firmware interface. \newline
2. Read accelerometer, gyroscope, and distance values while the drone remains stationary. \newline
3. Compare readings against expected physical conditions (e.g., gravity orientation for IMU, known distance for VLX). \\ \hline
\textbf{Test Analysis} & 
Sensors produced consistent readings within expected tolerances. Minor IMU biases were observed and could be corrected in firmware. Successful verification confirms sensors are ready for integration with control algorithms. \\ \hline
\end{tabular}
\end{table}

\begin{table}[H]
\centering
\renewcommand{\arraystretch}{1.2}
\begin{tabular}{|p{3.5cm}|p{12cm}|}
\hline
\textbf{Test No. \, 02} & \textbf{Motor Command Verification} \\ \hline
\textbf{Test Specification} & 
Validate that motor control commands are correctly transmitted and executed without flight. \\ \hline
\textbf{Test Description} & 
1. Connect the drone to WebSocket interface. \newline
2. Send incremental motor thrust commands while drone is fixed to a test rig. \newline
3. Monitor motor responses via telemetry and visually confirm expected rotation or PWM feedback. \\ \hline
\textbf{Test Analysis} & 
All motor commands were received and executed appropriately. Erratic behaviour was observed only under high throttle, suggesting a need for calibration. This confirms that motor control signals are correctly delivered by the firmware. \\ \hline
\end{tabular}
\end{table}

\begin{table}[H]
\centering
\renewcommand{\arraystretch}{1.2}
\begin{tabular}{|p{3.5cm}|p{12cm}|}
\hline
\textbf{Test No. \, 03} & \textbf{IMU Data Validation} \\ \hline
\textbf{Test Specification} & 
Confirm the accuracy of accelerometer and gyroscope data for use in state estimation and control algorithms. \\ \hline
\textbf{Test Description} & 
1. Keep the drone stationary and log accelerometer and gyroscope outputs. \newline
2. Tilt and rotate the drone slowly to produce controlled changes in orientation. \newline
3. Compare logged sensor data against expected physical motion and orientation. \\ \hline
\textbf{Test Analysis} & 
Sensor data corresponded closely with expected motion profiles. Small offsets were observed and noted for bias correction in the firmware. This validates that IMU measurements are reliable for state estimation and PID control integration. \\ \hline
\end{tabular}
\end{table}

\begin{table}[H]
\centering
\renewcommand{\arraystretch}{1.2}
\begin{tabular}{|p{3.5cm}|p{12cm}|}
\hline
\textbf{Test No. \, 04} & \textbf{R.30 - Disconnection Response} (Firmware) \\ \hline
\textbf{Test Specification} & 
Ensure the drone powers off safely after loss of connection, observing motor shutdown and null setpoints. \\ \hline
\textbf{Test Description} & 
1. Connect drone to WebSocket interface. \newline
2. Send setpoints and verify terminal output. \newline
3. Close the control webpage to simulate disconnection. \newline
4. Observe if the drone detects disconnection and motors shut off. \\ \hline
\textbf{Test Analysis} & 
The drone successfully detected the disconnection and immediately ceased motor activity. This confirms proper handling of lost connection and application of null setpoints, meeting R.30. \\ \hline
\end{tabular}
\end{table}

\begin{table}[H]
\centering
\renewcommand{\arraystretch}{1.2}
\begin{tabular}{|p{3.5cm}|p{12cm}|}
\hline
\textbf{Test No. \, 05} & \textbf{R.3 - WebSocket State Estimate} (Firmware) \\ \hline

\textbf{Test Specification} & 
Validate the state estimation algorithm by comparing measured drone orientation with computed estimates. \\ \hline

\textbf{Test Description} & 
1. Tilt and manipulate drone manually while connected to WebSocket. \newline
2. Monitor state estimate output and compare with actual drone movements. \\ \hline

\textbf{Test Analysis} & 
The algorithm accurately tracked the drone's orientation under moderate movements. Rapid changes introduced minor lag and drift over time, indicating acceptable performance within normal operational limits. \\ \hline
\end{tabular}
\end{table}

%-------------------------------------------------------------%
\paragraph{Dynamic Testing} \leavevmode

Evaluated system-level performance including lift-off, hovering, and control tuning. Although sustained flight was not achieved, these tests revealed essential insights for future iteration — particularly regarding motor alignment and PID tuning. 

\begin{table}[H]
\centering
\renewcommand{\arraystretch}{1.2}
\begin{tabular}{|p{3.5cm}|p{12cm}|}
\hline
\textbf{Test No. \, 06} & \textbf{R.2 - Capable of Hovering} (Hardware/Firmware) \\ \hline
\textbf{Test Specification} & 
Validate that the drone can lift and maintain altitude, assessing motor thrust, PID control, and manual tuning. \\ \hline
\textbf{Test Description} & 
1. Connect drone to WebSocket interface. \newline
2. Gradually increase thrust with PID disabled until lift-off occurs. \newline
3. Observe behaviour at higher thrust levels. \newline
4. Re-enable PID and attempt manual tuning of pitch/roll gains to assess stabilisation. \\ \hline
\textbf{Test Analysis} & 
The drone achieved lift-off; however, uneven thrust caused flipping tendencies at higher throttle. PID control did not improve stability, and manual tuning produced the same result. Likely causes include thrust misalignment or motor calibration errors rather than PID tuning. \\ \hline
\end{tabular}
\end{table}

\begin{table}[H]
\centering
\renewcommand{\arraystretch}{1.2}
\begin{tabular}{|p{3.5cm}|p{12cm}|}
\hline
\textbf{Test No. \, 07} & \textbf{R.4 / R.2 - Hovering and Altitude Maintenance} (Hardware/Firmware) \\ \hline
\textbf{Test Specification} & 
Assess the drone's ability to achieve and maintain a stable hover at set altitude. \\ \hline
\textbf{Test Description} & 
Attempt hover with PID stabilisation active, monitoring altitude and control response via WebSocket. \\ \hline
\textbf{Test Analysis} & 
Hover could not be maintained due to instability. This prevented altitude evaluation and suggests issues with motor output consistency or control tuning. \\ \hline
\end{tabular}
\end{table}

\begin{table}[H]
\centering
\renewcommand{\arraystretch}{1.2}
\begin{tabular}{|p{3.5cm}|p{12cm}|}
\hline
\textbf{Test No. \, 08} & \textbf{R.20 - Flight Stabilisation} (Hardware/Firmware) \\ \hline
\textbf{Test Specification} & 
Evaluate PID-based stabilisation and control signal application during flight. \\ \hline
\textbf{Test Description} & 
Monitor control signals and motor output during hovering attempts, observing PID response and integral windup. \\ \hline
\textbf{Test Analysis} & 
Hover could not be achieved, limiting assessment. Control signals were active and adjusted, but incomplete testing prevented full stabilisation. Integral windup was noted, but this likely occurred because stable flight couldn't be achieved. \\ \hline
\end{tabular}
\end{table}

%-------------------------------------------------------------%
\subsubsection{Outcome of Testing} \leavevmode

Overall, testing verified functional integration between hardware and firmware components. Sensor readings, communication interfaces, and power regulation behaved as intended. Dynamic flight tests confirmed lift capability but revealed instability attributed to motor thrust imbalance and tuning parameters. No critical hardware failures were observed. The tests collectively demonstrate a successful proof of concept and provide a clear direction for future refinement in control tuning and propulsion calibration.

The results of these tests are current as of the submission of this report. Tests covering the full set of requirements is provided in Appendix~\ref{app:v-and-v}, which includes the Verification and Validation table used to assess the final product. Any updates to this table up to the day of the demonstration will be made available on GitHub at~\cite{flightcontroller_git}.

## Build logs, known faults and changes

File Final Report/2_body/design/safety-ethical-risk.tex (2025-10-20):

\subsection{Safety Issues}
This safety plan applies to bench electronics work, soldering and rework, and controlled indoor hover testing. All activities are conducted in designated laboratory spaces with restricted access during active testing. Risk ratings follow a consequence–likelihood–exposure (C×L×E) model. Mitigations apply the hierarchy of hazard control: elimination, substitution, engineering control, administrative control, and PPE as a final layer. Full details are contained in the risk register.

\vspace{0.5em}
\textbf{Operational Boundaries and Controls:}

\begin{tabular}{|p{4cm}|p{11.5cm}|}
\hline
\rowcolor{gray!15}\textbf{Aspect} & \textbf{Defined Limits and Requirements} \\ \hline
Environment & Indoor test room only; access restricted during hover tests with signage placed outside. \\ \hline
Training & All personnel must complete soldering and \gls{lipo} handling inductions before handling any equipment. \\ \hline
Hover Testing & Hover altitude limited to 1.25\,m AGL; any adjustment beyond this permitted only during setup phases with props disarmed. \\ \hline
Battery Management & Only 1S/2S \gls{lipo} <800\,mAh packs approved; no swollen or damaged cells. Charging supervised with fire blanket or sand bucket available. \\ \hline
Personnel & Minimum two people: Test Lead with authority to abort and Spotter monitoring environmental conditions and escape paths. \\ \hline
PPE & Safety glasses and closed footwear mandatory at all times; nitrile gloves required for chemical or flux handling tasks. \\ \hline
\end{tabular}

\vspace{0.5em}
\textbf{Acceptance Criteria:} All tests must demonstrate thermal compliance, fail-safe functionality, clean electrical behaviour, and incident-free operation. Logs and checklists must be completed to satisfy traceability requirements.

The following table summarises key hazards, their associated risks, and control approaches.

\begin{tabular}{|p{2.3cm}|p{4.5cm}|p{4cm}|p{3.8cm}|}
\hline
\rowcolor{gray!15}\textbf{Hazard} & \textbf{Risks/Mechanism} & \textbf{Controls Implemented} & \textbf{Procedure} \\ \hline
Heating & Localised MOSFET heating or soldering burns & Copper pours, current limiting, heat mats & IR checks, switch-off when idle \\ \hline
Cuts/Abrasions & Propeller lacerations or tool injuries & Shrouds, guarded tools, PPE & Bench test first, enable arming \gls{led} cues \\ \hline
Sparking & Short circuits or solder bridging & Heat-shrink, clearance design & continuity test, no live soldering \\ \hline
Battery & Thermal runaway or over-discharge & Voltage alarms, visual inspection & Remove damaged cells, fire control kit on-site \\ \hline
Trips/Spills & Loose cables/liquids in walkways & Cable trays, dry floor policy & End-of-session clearance audit \\ \hline
Collisions & Impact during hover test & Altitude limit, prop shields & Incident log, abort protocol \\ \hline
Fumes & Flux fumes, UFPs from printing & Extraction fans, gloves & Ventilation check, SDS access \\ \hline
\end{tabular}

%-------------------------------------------------------------% 
\pagebreak
\subsection{Ethical Issues}
Testing takes place in a shared laboratory environment, so ethical considerations focus on safety, responsible data handling, and clear usage boundaries for open-source release. Exclusion zones will be clearly marked, and written approval is obtained from space owners before any powered testing. A spotter is always present to ensure that no unauthorised person enters the test area.

\vspace{0.5em}
\textbf{Data and Recording:}  
The onboard camera remains disabled by default and is only activated during scheduled and approved hover trials. Any footage containing identifiable individuals will require written consent before capture. Recordings, if taken, are stored in encrypted form, retained for no longer than seven days and permanently deleted upon request.

\vspace{0.5em}
\textbf{Wireless Communication:}  
Wi-Fi telemetry operates under least-privilege access principles. No personal device identifiers are logged. \gls{rf} transmissions remain within laboratory and local regulatory limits. Channels that may conflict with co-located research equipment are excluded.

\vspace{0.5em}
\textbf{Open-Source Release and Responsible Use:}  
All CAD, firmware, and PCB files will be published under a permissive open-source license. Documentation will clearly state:

\begin{itemize}
    \item Intended operation is indoor hover testing only, with shrouded rotors and fully functional fail-safes.
    \item Prohibited uses include surveillance without explicit consent, public outdoor operation, weaponisation, or disabling of safety systems.
    \item Recommended safe substitution components, correct \gls{lipo} disposal procedures, and repair instructions using reprintable \gls{petg} parts.
\end{itemize}

This ensures that any derivative builds acknowledge ethical and safety boundaries aligned with the project's academic intent.

%-------------------------------------------------------------% 
\pagebreak
\subsection{Top 5 Risks and Mitigations}

The following risks have the highest inherent risk ranking based on (C×L×E). Mitigations follow the hierarchy of controls, and each risk includes a defined verification test to confirm that controls are effective.

\textbf{RISK-01: Slips \& Trips}

\begin{tabular}{@{}p{3cm}p{13cm}@{}}
\toprule
\textbf{Inherent Risk} & 1500 (Very High) \\
\textbf{Key Causes} & Loose cables, tools obstructing walkways, congested bench area. \\
\textbf{Mitigations} &
• \textbf{Elimination:} Keep walkways clear, remove floor clutter. \newline
• \textbf{Engineering:} Use cable trays, tape down leads. \newline
• \textbf{Administrative:} End-of-session clearance checks, clear-aisle policy. \newline
• \textbf{PPE:} Closed-toe footwear. \\
\textbf{Verification Test} & Walkway audit: zero loose cables/tools; aisles $\geq$900\,mm clear. Pass, no hazards found \\
\textbf{Residual Risk} & Low \\
\bottomrule
\end{tabular}
\vspace{0.6em}

\textbf{RISK-02: Poor Ventilation / Asphyxiation}

\begin{tabular}{@{}p{3cm}p{13cm}@{}}
\toprule
\textbf{Inherent Risk} & 750 (Very High) \\
\textbf{Key Causes} & Soldering without fume extraction; extended work in enclosed areas. \\
\textbf{Mitigations} &
• \textbf{Substitution:} Use low-odour, rosin-free flux. \newline
• \textbf{Engineering:} Enable local fume extraction with filters. \newline
• \textbf{Administrative:} Ventilation checks before work, time limits on solder tasks. \newline
• \textbf{PPE:} Optional respirator if extraction unavailable. \\
\textbf{Verification Test} & Fume extractor active, filter in place, ventilation checklist signed. Pass, all conditions met \\
\textbf{Residual Risk} & Low \\
\bottomrule
\end{tabular}
\vspace{0.6em}

\textbf{RISK-03: Cuts / Abrasions}

\begin{tabular}{@{}p{3cm}p{13cm}@{}}
\toprule
\textbf{Inherent Risk} & 450 (High) \\
\textbf{Key Causes} & Sharp tools or part edges, damaged 3D prints or PCBs. \\
\textbf{Mitigations} &
• \textbf{Elimination:} Deburr and smooth printed/metal edges. \newline
• \textbf{Engineering:} Use tool guards and retractable blades. \newline
• \textbf{Administrative:} Tool-use training and blade return protocol. \newline
• \textbf{PPE:} Safety glasses; cut-resistant gloves if needed. \\
\textbf{Verification Test} & All sharp edges smoothed; blades stored safely; PPE worn during cutting. Pass, all conditions met \\
\textbf{Residual Risk} & Low \\
\bottomrule
\end{tabular}
\vspace{0.6em}

\pagebreak
\textbf{RISK-04: Burns (Soldering / Hot Components)}

\begin{tabular}{@{}p{3cm}p{13cm}@{}}
\toprule
\textbf{Inherent Risk} & 450 (High) \\
\textbf{Key Causes} & Contact with hot soldering iron tips or overheated MOSFETs. \\
\textbf{Mitigations} &
• \textbf{Engineering:} Use tip stands and heat-proof mats. \newline
• \textbf{Administrative:} Do not leave powered irons unattended. \newline
• \textbf{PPE:} Safety glasses; heat-resistant gloves if required. \\
\textbf{Verification Test} & Iron stored in stand; heat mat in use; motor driver $<85^\circ$C after 5\,min hover. Pass, all conditions true \\
\textbf{Residual Risk} & Low \\
\bottomrule
\end{tabular}
\vspace{0.6em}

\textbf{RISK-05: Emissions (Solder / 3D-Print Fumes)}

\begin{tabular}{@{}p{3cm}p{13cm}@{}}
\toprule
\textbf{Inherent Risk} & 270 (Medium) \\
\textbf{Key Causes} & Flux fumes, ultrafine particle emissions from filament heating. \\
\textbf{Mitigations} &
• \textbf{Substitution:} Lead-free solder and low-emission filament. \newline
• \textbf{Engineering:} Local fume extraction for soldering and printing. \newline
• \textbf{Administrative:} Store chemicals sealed; SDS available. \newline
• \textbf{PPE:} Safety glasses; nitrile gloves for solvent handling. \\
\textbf{Verification Test} & Extraction active and SDS visible; PPE worn when handling resin/solvents. Pass, all conditions true \\
\textbf{Residual Risk} & Low \\
\bottomrule
\end{tabular}

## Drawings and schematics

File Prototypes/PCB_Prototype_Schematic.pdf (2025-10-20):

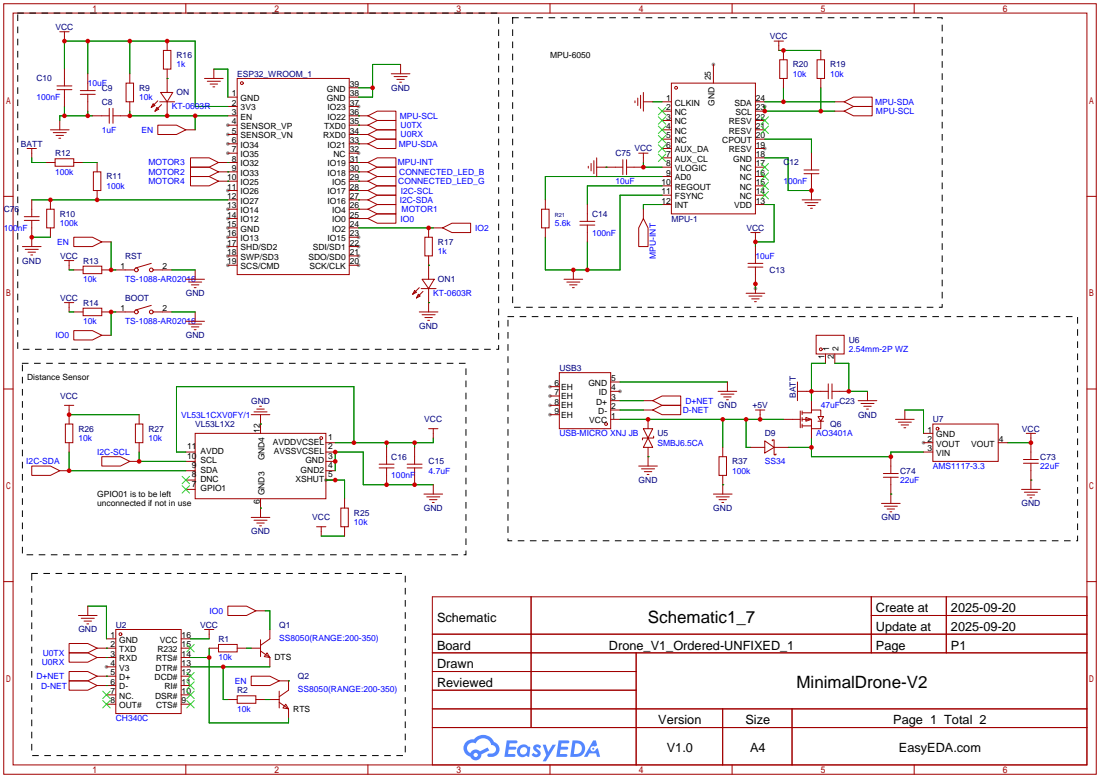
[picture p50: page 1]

GPIO01 is to be left
unconnected if not in use

Schematic | Schematic1_7 | Create at | 2025-09-20

Update at | 2025-09-20

DSR# 10 RI# 11 DCD# 12 DTR# 13 RTS# 14 R232 15 VCC 16

Board | Drone_V1_Ordered-UNFIXED_1 | Page | P1
Drawn | | MinimalDrone-V2
Reviewed

Version | Size | Page 1 Total 2
V1.0 | A4 | EasyEDA.com

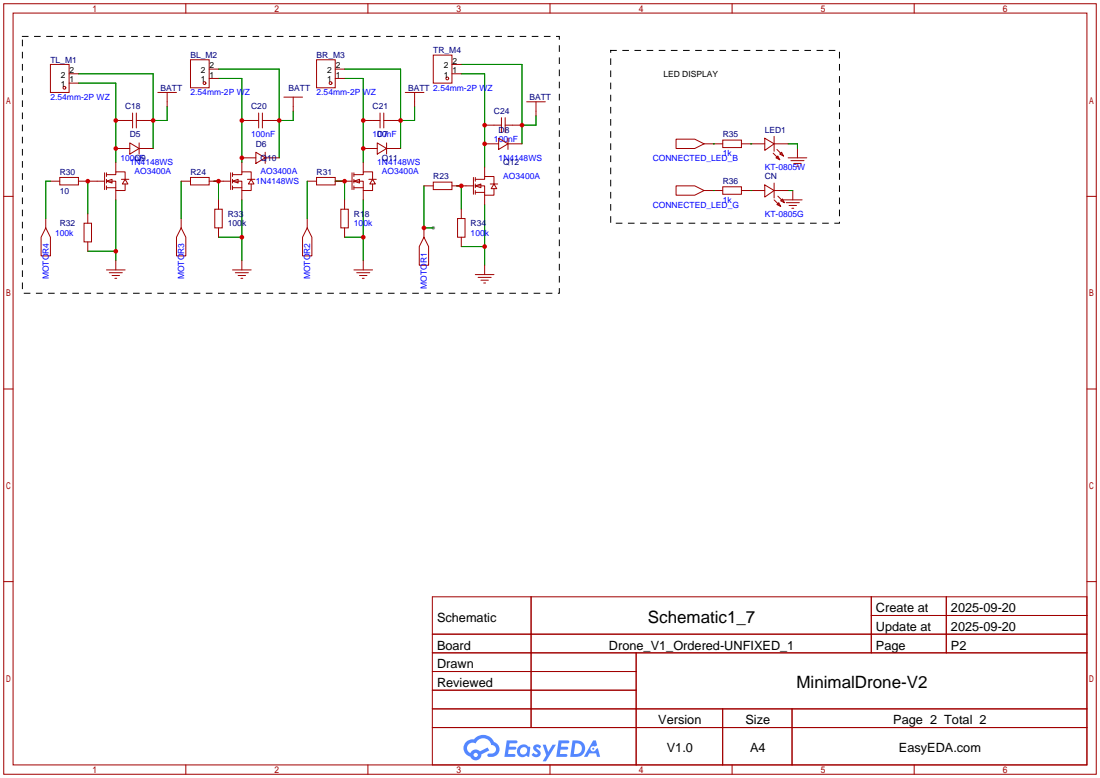
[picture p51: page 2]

Schematic | Schematic1_7 | Create at | 2025-09-20

Update at | 2025-09-20

Board | Drone_V1_Ordered-UNFIXED_1 | Page | P2
Drawn | | MinimalDrone-V2
Reviewed

Version | Size | Page 2 Total 2
V1.0 | A4 | EasyEDA.com

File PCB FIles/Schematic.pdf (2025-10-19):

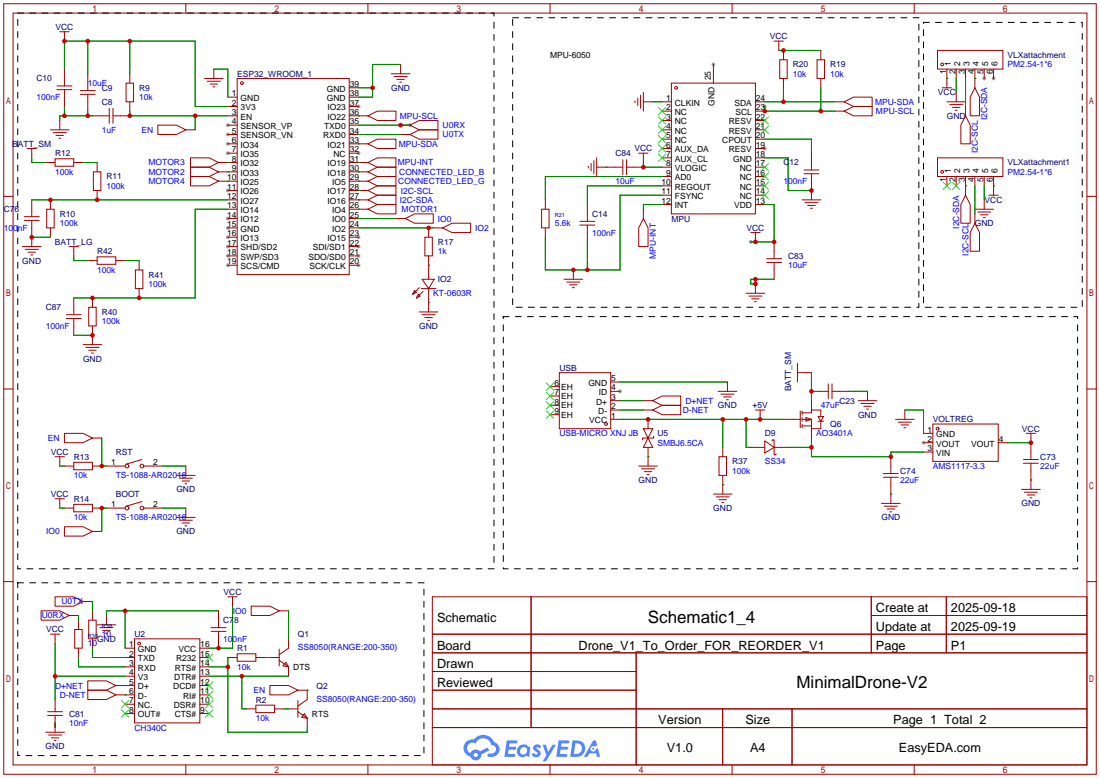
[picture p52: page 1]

Schematic | Schematic1_4 | Create at | 2025-09-18

Update at | 2025-09-19

Board | Drone_V1_To_Order_FOR_REORDER_V1 | Page | P1
Drawn | | MinimalDrone-V2
Reviewed

DSR# 10 RI# 11 DCD# 12 DTR# 13 RTS# 14 R232 15 VCC 16

Version | Size | Page 1 Total 2
V1.0 | A4 | EasyEDA.com

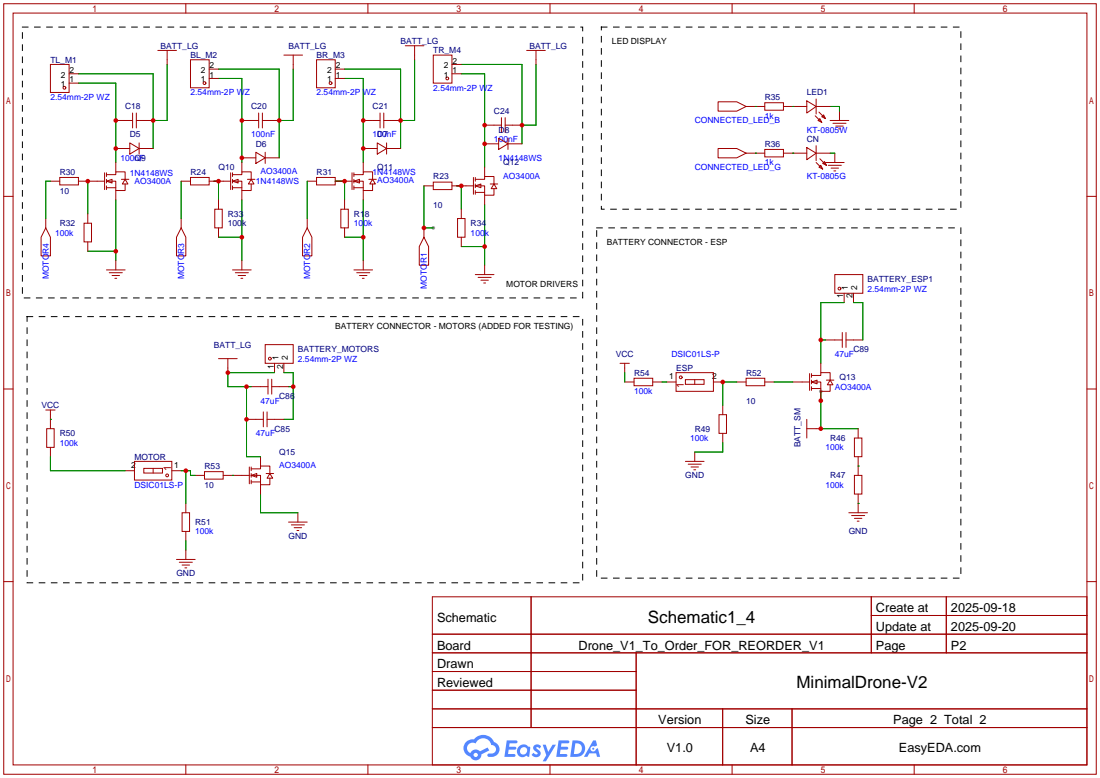
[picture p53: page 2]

BATTERY CONNECTOR - MOTORS (ADDED FOR TESTING)

Schematic | Schematic1_4 | Create at | 2025-09-18

Update at | 2025-09-20

Board | Drone_V1_To_Order_FOR_REORDER_V1 | Page | P2
Drawn | | MinimalDrone-V2
Reviewed

Version | Size | Page 2 Total 2
V1.0 | A4 | EasyEDA.com

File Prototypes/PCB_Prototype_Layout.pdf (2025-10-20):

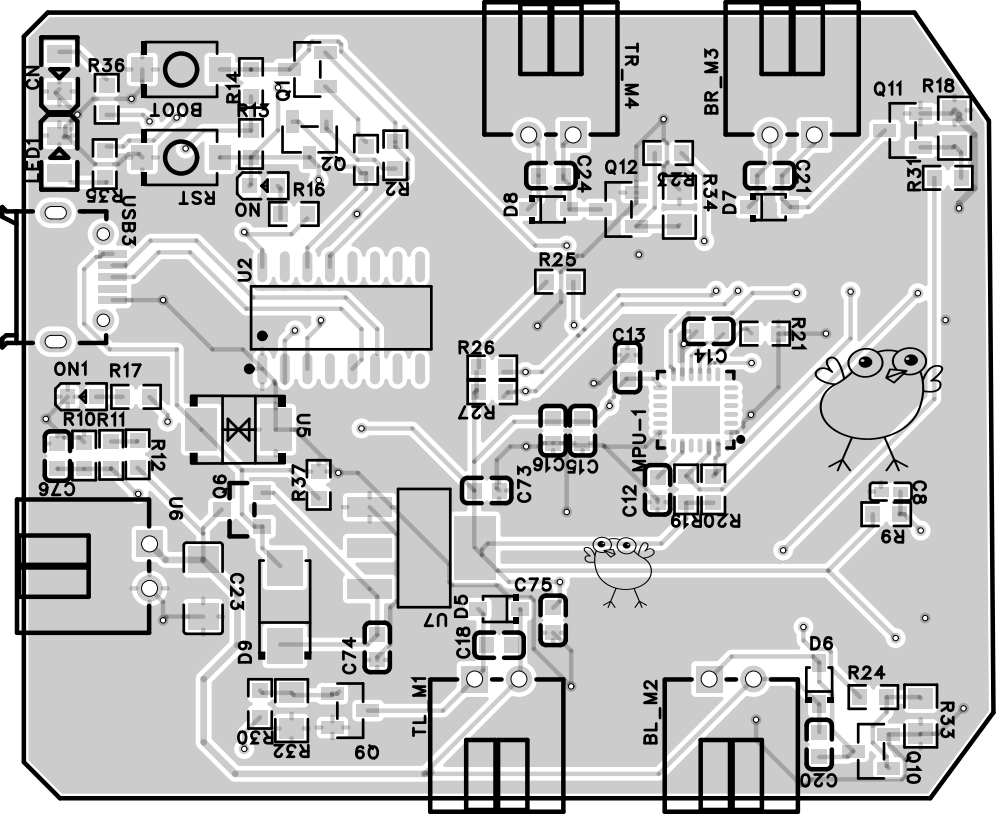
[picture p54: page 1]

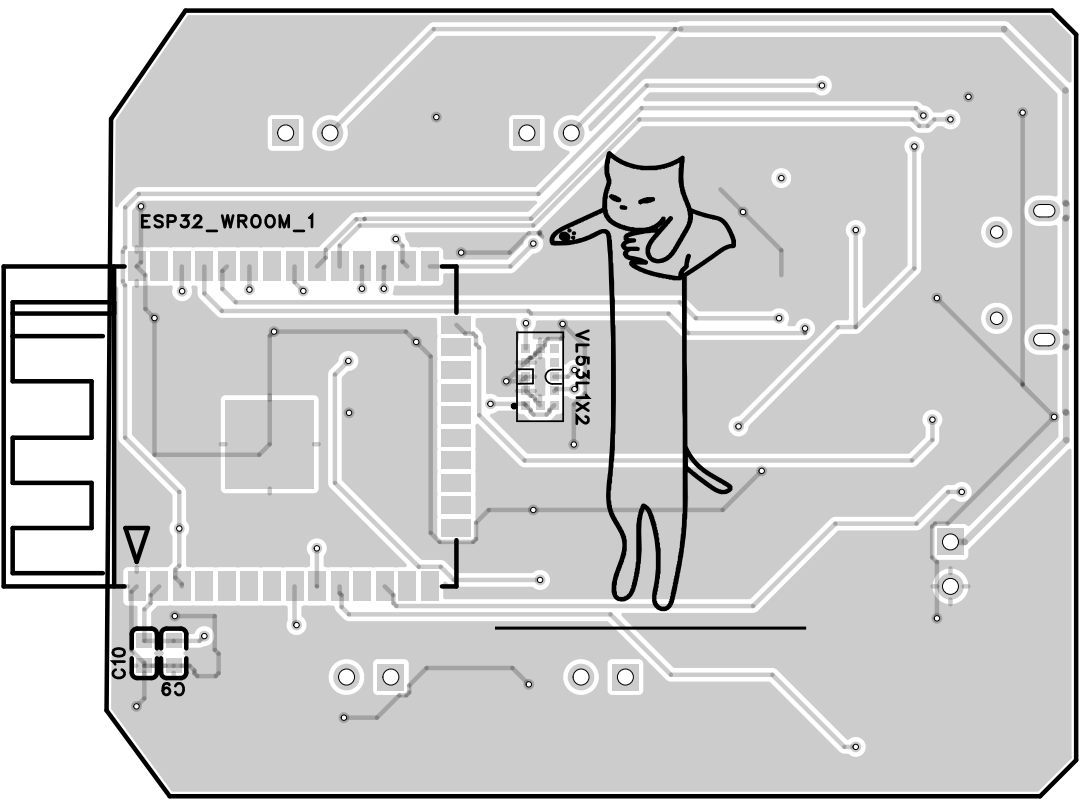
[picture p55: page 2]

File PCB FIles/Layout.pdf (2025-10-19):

# R24 R30 R³¹

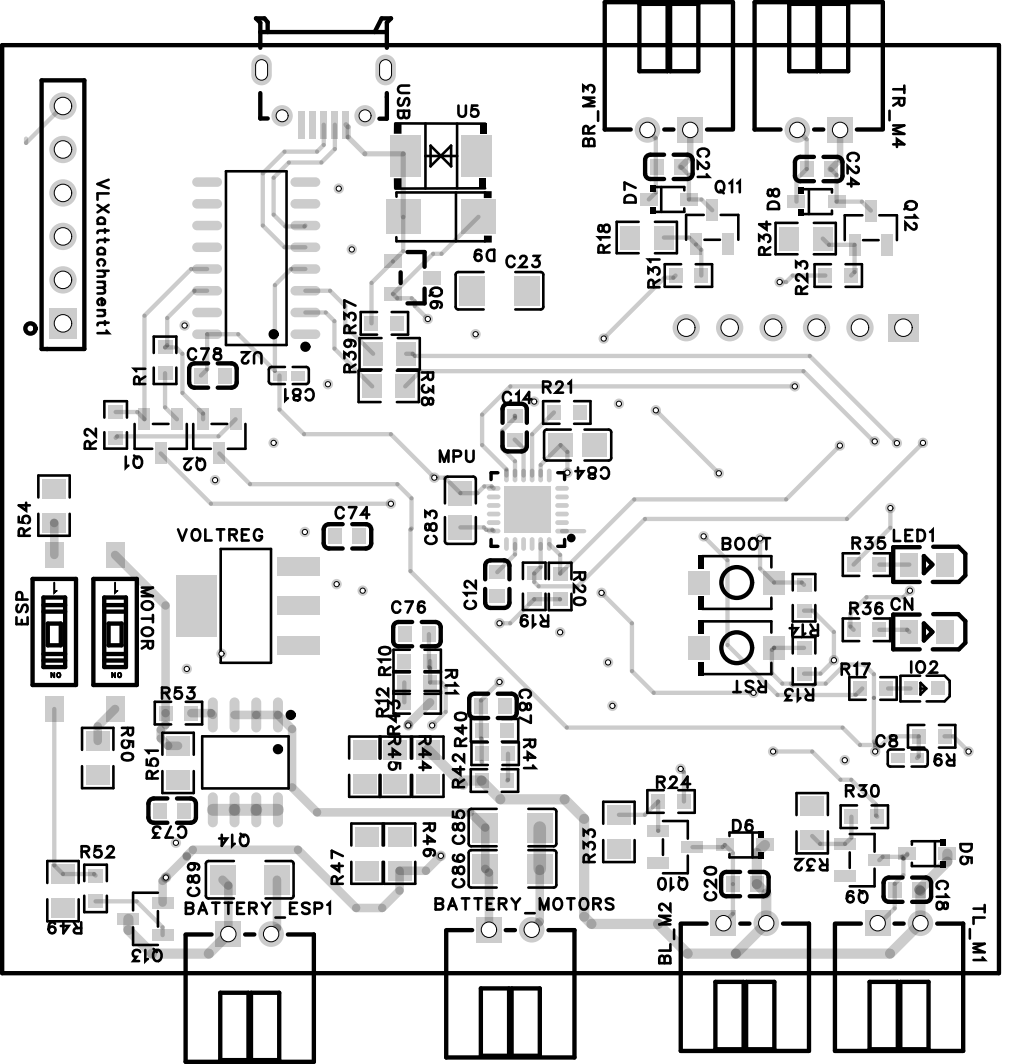
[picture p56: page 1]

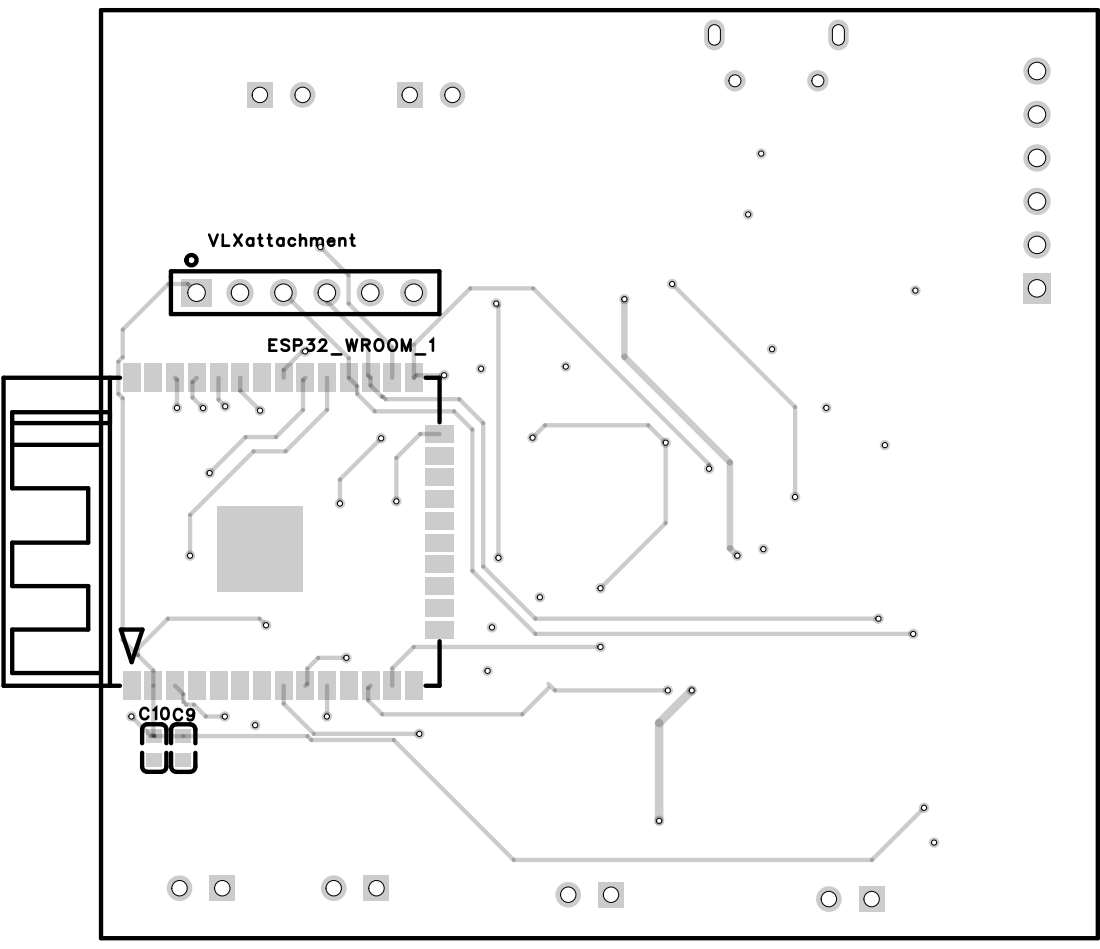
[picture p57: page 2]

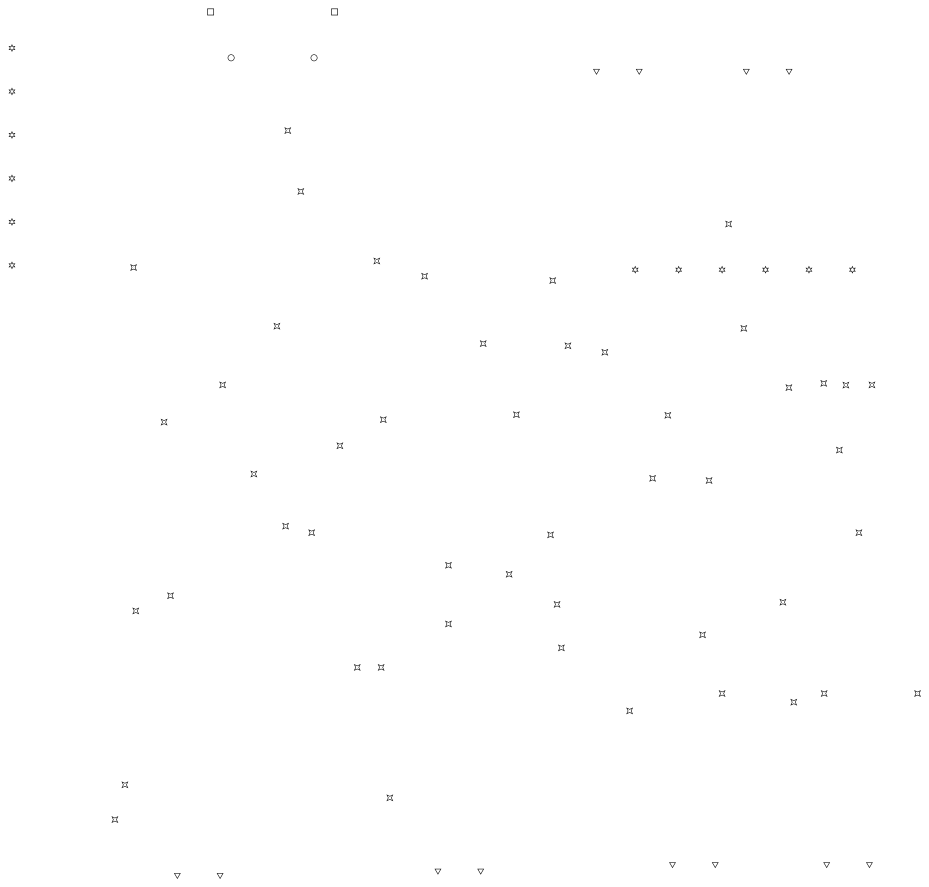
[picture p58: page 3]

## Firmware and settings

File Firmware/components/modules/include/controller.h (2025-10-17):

#ifndef CONTROLLER_H_
#define CONTROLLER_H_

#include <stdbool.h>
#include <stdint.h>
#include "filter.h"
#include "sensors.h"
#include "stabiliser.h"

// PID constants
#define PID_ROLL_RATE_KP  100.0
#define PID_ROLL_RATE_KI  0
#define PID_ROLL_RATE_KD  0
#define PID_ROLL_RATE_INT_LIMIT 33.3

#define PID_PITCH_RATE_KP  100.0
#define PID_PITCH_RATE_KI  0
#define PID_PITCH_RATE_KD  0
#define PID_PITCH_RATE_INT_LIMIT 33.3

#define PID_YAW_RATE_KP  50.0
#define PID_YAW_RATE_KI  0
#define PID_YAW_RATE_KD  0
#define PID_YAW_RATE_INT_LIMIT 166.7

#define PID_ROLL_KP  2
#define PID_ROLL_KI  0
#define PID_ROLL_KD  0.0
#define PID_ROLL_INT_LIMIT 20.0

#define PID_PITCH_KP  2
#define PID_PITCH_KI  0
#define PID_PITCH_KD  0.0
#define PID_PITCH_INT_LIMIT 20.0

#define PID_YAW_KP  2
#define PID_YAW_KI  0
#define PID_YAW_KD  0
#define PID_YAW_INT_LIMIT 360.0

#define DEFAULT_PID_INT_LIMIT 5000.0
#define DEFAULT_PID_OUT_LIMIT 0.0

#define ATT_LPF_FC 15.0f
#define ATT_LPF_EN true
#define ATT_RATE_LPF_FC 30.0f
#define ATT_RATE_LPF_EN true

#define THRUST_MIN 0
#define THRUST_MAX 65535

typedef struct
{
  float desired;
  float error;
  float prev_error;
  float integ;
  float deriv;
  float kp;
  float ki;
  float kd;
  float out_p;
  float out_i;
  float out_d;
  float int_limit;
  float out_limit;
  float dt;
  lpf_data d_filter;
  bool d_filter_en;
} PidObject;

void controllerInitPID(void);
void controllerPID(sensor_data_t *sensor, state_t *state, setpoint_t *setpoint, control_t *control, const uint32_t tick);
void pidInit(PidObject* pid, float desired, float kp, float ki, float kd, float dt, float fs, float fc, bool en_filter);
float pidUpdate(PidObject* pid, float measured, bool update_error);
void positionController(float *thrust, attitude_t *att_desired, setpoint_t *setpoint, state_t *state);
float angleLimit(float angle);
int16_t saturateSignedInt16(float in);
float constrain(float value, const float minVal, const float maxVal);
float scaleThrust(float actuator_thrust);
float scaleAngle90(float setpoint);
float scaleAngle180(float setpoint);

#endif

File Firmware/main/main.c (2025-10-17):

#include <stdio.h>
#include "sdkconfig.h"
#include "freertos/FreeRTOS.h"
#include "freertos/task.h"
#include "esp_log.h"

#include "i2c.h"
#include "sensors.h"
#include "websocket.h"
#include "stabiliser.h"

void app_main(void)
{
    sensor_task_init();
    vTaskDelay(pdMS_TO_TICKS(2000));
    websocket_task_init();
    vTaskDelay(pdMS_TO_TICKS(2000));
    stabiliserTaskInit();
}

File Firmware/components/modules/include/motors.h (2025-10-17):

#ifndef MOTORS_H_
#define MOTORS_H_

#include <stdint.h>
#include <stdbool.h>
#include "stabiliser.h"

#define DEFAULT_IDLE_THRUST 0

#define NBR_OF_MOTORS 4
#define MOTOR_M1  0
#define MOTOR_M2  1
#define MOTOR_M3  2
#define MOTOR_M4  3

#define MOTOR1_GPIO  4
#define MOTOR2_GPIO  33
#define MOTOR3_GPIO  32
#define MOTOR4_GPIO  25

#define MOT_PWM_CH1  4
#define MOT_PWM_CH2  5
#define MOT_PWM_CH3  6
#define MOT_PWM_CH4  7

#define MOTORS_PWM_BITS           LEDC_TIMER_8_BIT
#define MOTORS_PWM_PERIOD         ((1<<MOTORS_PWM_BITS) - 1)
#define MOTORS_TIM_BEEP_CLK_FREQ  4000000

#define MOTORS_TEST_RATIO         (uint16_t)(0.2*(1<<16))
#define MOTORS_TEST_ON_TIME_MS    50
#define MOTORS_TEST_DELAY_TIME_MS 150

void motorsInit(void);
void motorsDeInit(void);
void motorsSetRatio(uint32_t id, uint16_t ithrust);
void powerDistribution(const control_t *control);
bool motorsTest(void);
bool powerDistributionTest(void);
void motorsInit(void);
void motorsDeInit(void);
bool PWMTimerInit(void);
uint16_t limitUint16(int32_t value);
uint16_t motorsConvBitsTo16(uint16_t bits);
uint16_t motorsConv16ToBits(uint16_t bits);

#endif

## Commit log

2025-10-17 Added final report latex and current firmware
    [partitions.csv]
2025-10-17 Added testing and assembly
2025-10-19 Added PCB and frame
    [BOM_Drone_V1_To_Order_no button for reorder_PCB23_1_2025-10-19.xlsx, PickAndPlace_PCB.xlsx, battery_cage.stl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]
2025-10-20 Finalising changes and outputs
    [BOM_Drone_V1_To_Order_no button for reorder_PCB23_1_2025-10-19.xlsx, OldFrame_fitsPBC2 1.stl, OldFrame_fitsPBC2 2.stl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]
2025-10-20 Fixed v&v
    [RequirementsReview.xlsx]
2025-10-20 Fixed v&v again
    [RequirementsReview.xlsx]
